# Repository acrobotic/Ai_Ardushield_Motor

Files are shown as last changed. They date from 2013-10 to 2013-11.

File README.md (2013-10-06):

Overview
---
This repository includes the Eagle design files (schematics and layout) for our
[Motor Shield for the Arduino Uno][1]. The shield design is based on two ICs:
the Toshiba TB6612FNG dual motor driver and the NXP PCA9685 16-bit PWM
generator.  The TB6612FNG uses the PWM signals generated by the PCA9685 to set
the speed and direction of the motor(s) connected to its output.  The PWM
signals are set by the commands sent from the Arduino to the PCA9685
via I2C.

The shield includes 2 motor driver chips, so it's able to control up to 4
bi-directional DC motors, 2 stepper motors (uni- or bi-polar), or a combination
of the two types.  

The PWM chip is controlled via I2C, which allows the shield to be stackable.
By setting each shield on the stack to a different I2C address we can control
(in theory) up to 32 of these shields with a single Arduino.

A couple of standard 3-pin headers are readily available on the board for
connecting servo motors directly to pins D8 and D9 on the Arduino.

The firmware files along with code samples are also included in this
repository.

This product was heavily inspired by the [Adafruit Motor/Stepper/Servo Shield
for Arduino][2], and it's released under a (hopefully) compatible open-source
license detailed below.

Product page
---
Please consider buying products from Acrobotic to help fund future Open-Source
projects like this! We'll always put our best effort in every project, and
release all our design files and code for you to use.

[Tutorials, technical details, and more information about this product can be
found here: http://acrobotic.com/catalog/product/view/id/63][1]

License Information
---

All contents of this repository are licensed under a [Creative Commons
Attribution-ShareAlike 3.0 Unported
License](http://creativecommons.org/licenses/by-sa/3.0/).



[1]: http://acrobotic.com/catalog/product/view/id/63 "Ardushield Motor"
[2]: http://www.adafruit.com/products/1438 "Adafruit Motor/Stepper/Servo Shield for Arduino"

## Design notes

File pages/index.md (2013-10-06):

---
layout: page
title: Ai Ardushield Motor
tagline: Board design files and example firmware for the Acrobotic Motor Shield (Arduino Uno).
github_project: Ai_Ardushield_Motor
github_user_url: https://github.com/acrobotic
---
{% include JB/setup %}
{% include INCLUDE.md %}

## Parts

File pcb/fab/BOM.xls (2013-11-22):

Ai Ardushield Motor – BOM
Cisco Zabala (x1sc0@acrobotic.com) last updated: 22.11.2013
Manufacturer | Manuf. Part Number | Vendor | Vendor Part Number | Type | Designator | Qty | Description | Case | SMD, BGA, LCC, OR TH | Notes
Stackpole Electronics Inc | RMCF0603JT1K00 | Digi-Key | RMCF0603JT1K00CT-ND | Resistors | R1 | 1 | RES 1K OHM 1/10W 5% 0603 | 0603 | SMD
Stackpole Electronics Inc | RMCF0603JT10K0 | Digi-Key | RMCF0603JT10K0CT-ND |  | R2, R3, R4, R5, R6, R7, R8 | 7 | RES 10K OHM 1/10W 5% 0603 | 0603 | SMD
Panasonic Electronic Components | EEE-1CA101WP | Digi-Key | PCE3880CT-ND | Capacitors | C1 | 1 | CAP ALUM 100UF 16V 20% SMD | PANASONIC-C | SMD
Panasonic Electronic Components | EEE-1CA470WR | Digi-Key | PCE3890CT-ND |  | C2, C3 | 2 | CAP ALUM 47UF 16V 20% SMD | PANASONIC-C | SMD
Yageo | CC0603ZRY5V9BB104 | Digi-Key | 311-1343-1-ND |  | C4, C5, C6 | 3 | CAP CER 0.1UF 50V Y5V 0603 | 0603 | SMD
TDK Corporation | C1608X5R1A106M080AC | Digi-Key | 445-6853-1-ND |  | C7, C8 | 2 | CAP CER 10UF 10V 20% X5R 0603 | 0603 | SMD
NXP |  | Digi-Key | 568-5931-1-ND | ICs | IC1 | 1 | IC PWM CTLR LED DVR 28TSSOP | 28TSSOP | SMD
Toshiba |  | Digi-Key | TB6612FNG(OC8EL)CT-ND | IC | IC2, IC3 | 2 | IC MOTOR DRIVER PAR 24SSOP | 24SSOP | SMD
OSRAM | LB Q39E-N1P1-35-1 | Digi-Key | 475-2815-1-ND | LEDs | ON | 1 | LED CHIPLED BLUE 470NM 0603 SMD | 0603 | SMD
Alpha & Omega Semiconductor | AOD417 | Digi-Key | 785-1106-1-ND | Discrete | Q1 | 1 | MOSFET P-CH -30V -25A TO-252 | TO-252-3 | SMD
TE Connectivity | 2-1437565-9 | Digi-Key | 450-1792-1-ND | Buttons | SW1 | 1 | SWITCH TACTILE SPST-NO 0.05A 12V | 6mm x 6mm | SMD
 |  | Acrobotic | CON-00007 | Connectors | J1, J7, J8, J10 | 4 | 2-Pin Screw Terminal Block (3.5mm) |  | TH
 |  | Acrobotic | CON-00011 |  | J7, J8 | 2 | 3-Pin Screw Terminal Block (3.5mm) |  | TH
 |  | Acrobotic | CON-00010 |  | J2 | 1 | 0.1” Pitch, 2-Row, 6-Pin (Male) |  | TH
 |  | Acrobotic | CON-00009 |  | J3, J4, J5, J6, JP1. JP2 | 1-2 | 0.1” Pitch, 40-Pin (Male) |  | TH | Easily cut to length
 |  | - | - |  | J9 | - | - | - | - | Left open for user
 |  | Acrobotic | CON-00008 |  | (JP1, JP2) | 2 | 2-Pin Jumper |  | - | For power selection

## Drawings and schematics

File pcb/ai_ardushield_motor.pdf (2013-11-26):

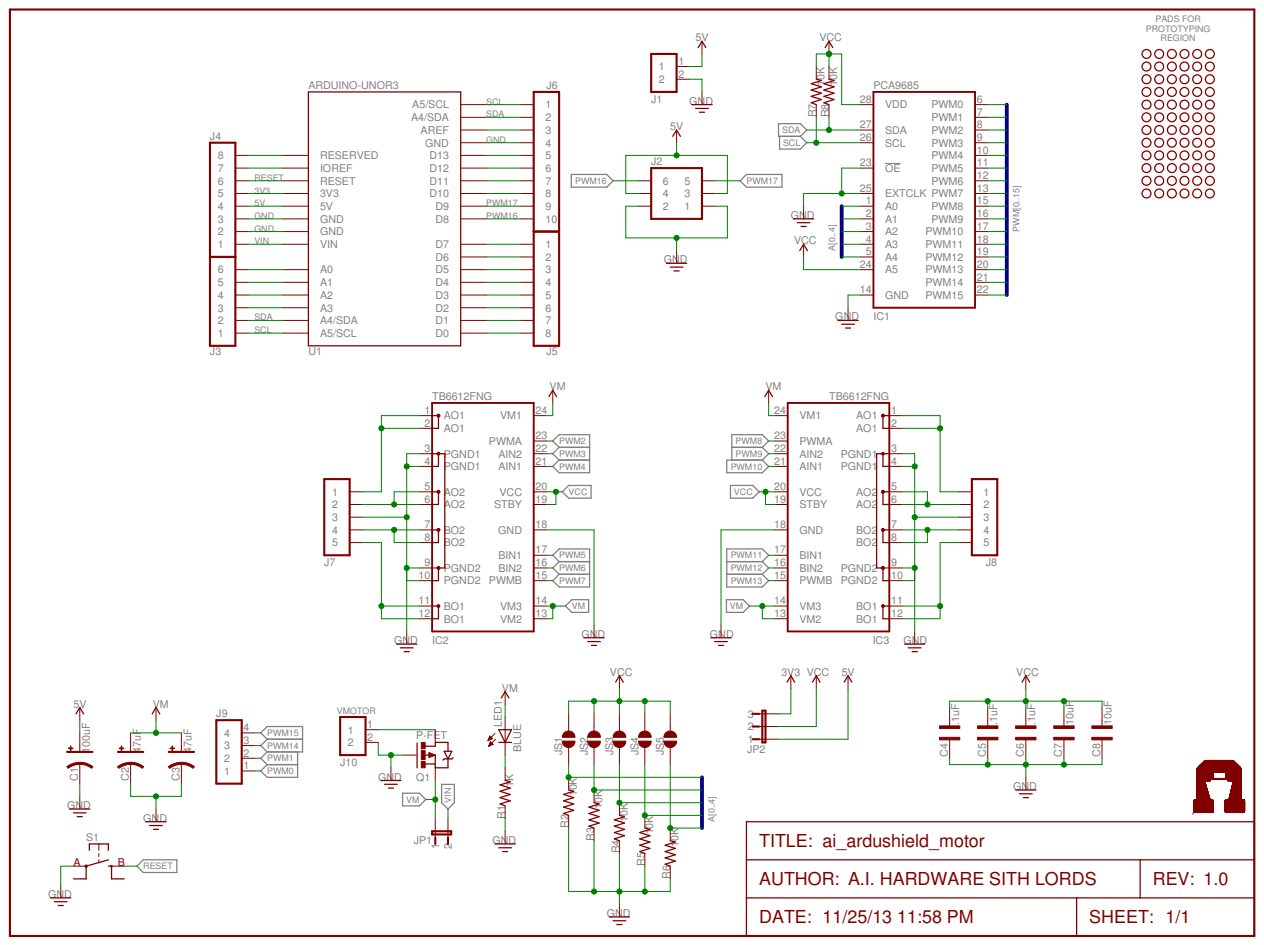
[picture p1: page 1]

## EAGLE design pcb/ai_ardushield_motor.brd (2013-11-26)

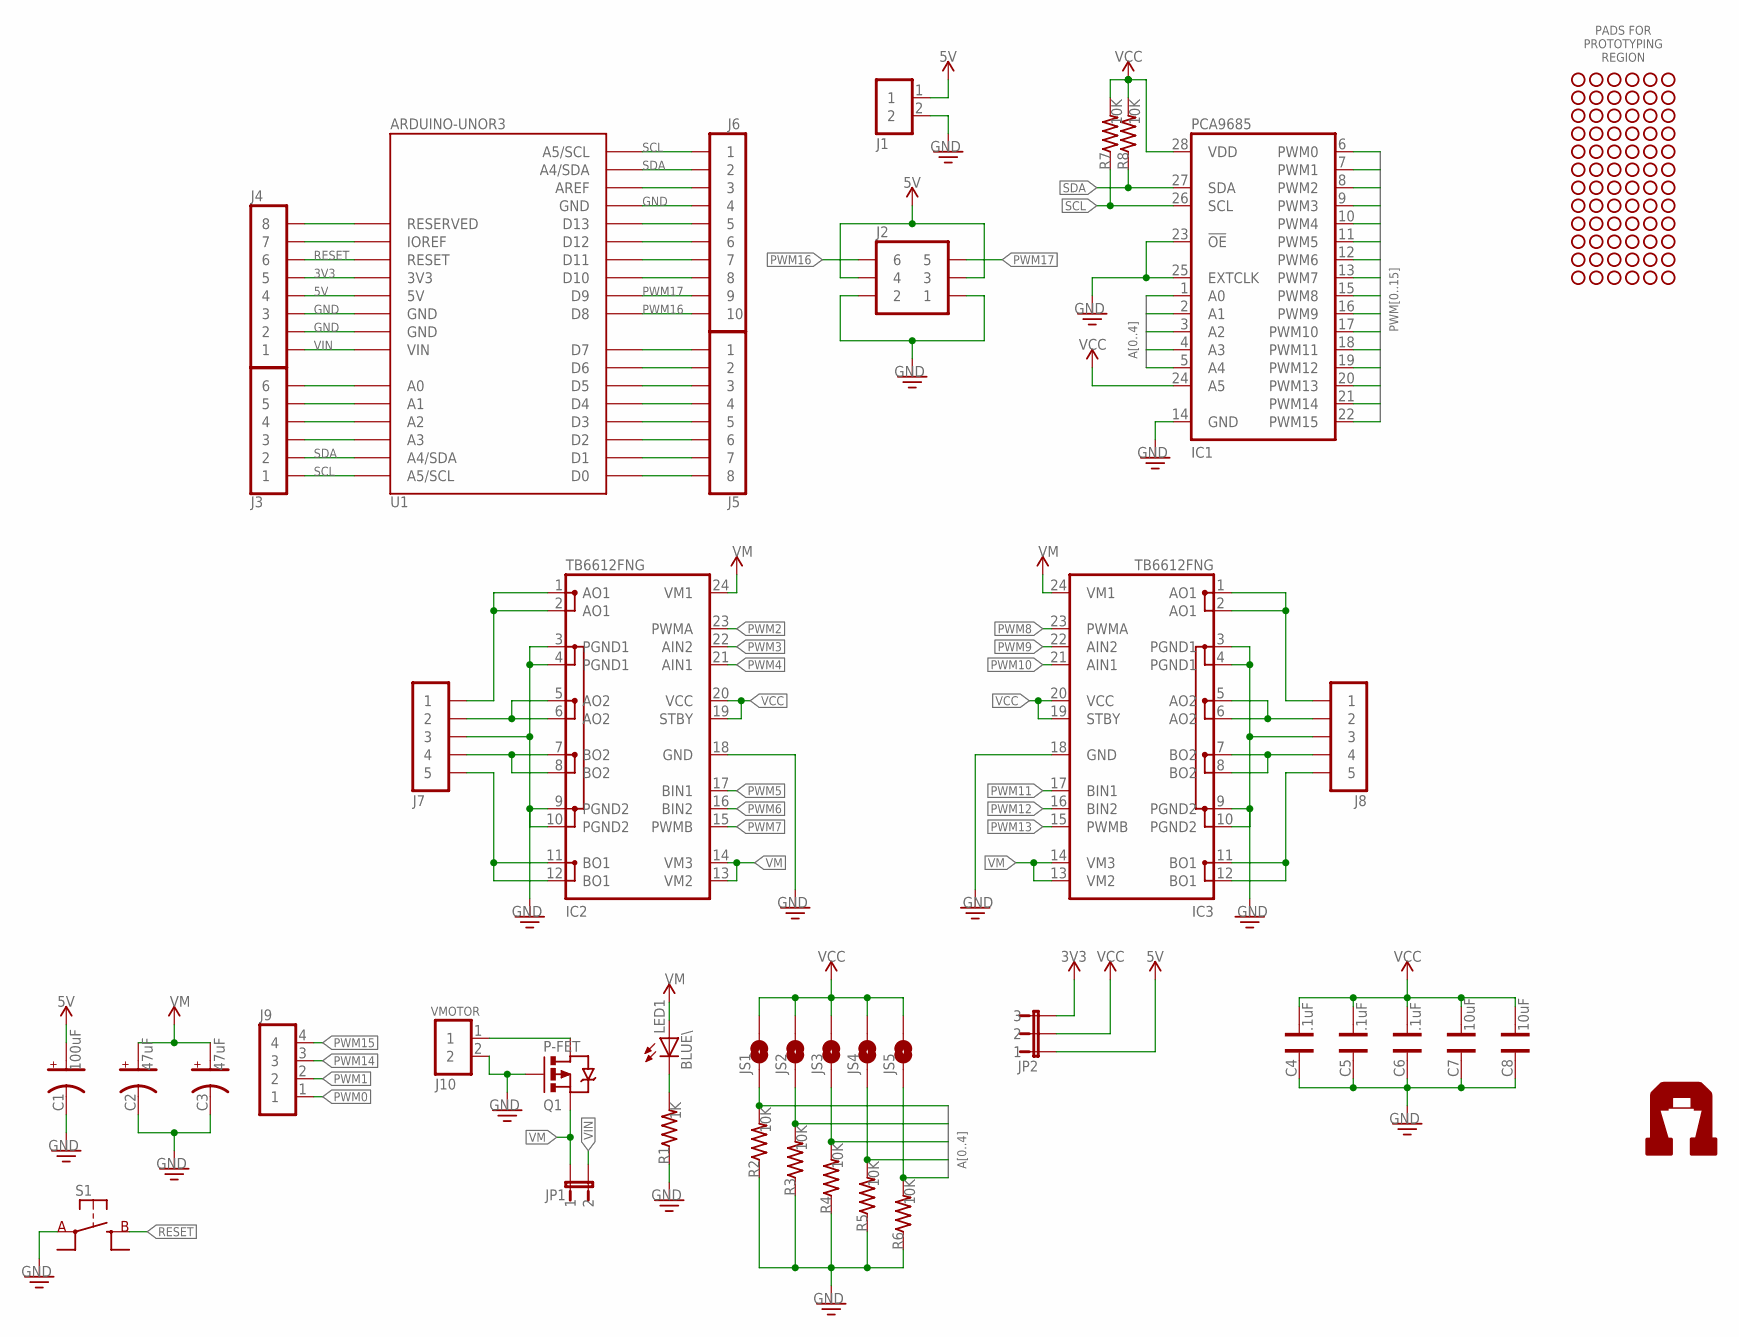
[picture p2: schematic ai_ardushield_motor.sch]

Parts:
C1: 100uF; CAP-PANASONIC-C
C2, C3: 47uF; CAP-PANASONIC-C
C4, C5, C6: .1uF; CAP-0603
C7, C8: 10uF; CAP-0603
IC1: PCA9685; TSSOP28
IC2, IC3: TB6612FNG; SSOP24
J1, J10: 1X02ST; 1X02-ST
J2: 2X03
J3: 1X06
J4, J5: 1X08
J6: 1X10
J7, J8: 1X05ST; 1X05-ST
J9: 1X04
J11, J12, J13, J14, J15, J16, J17, J18, J19, J20, J21, J22: 1X06-PROTO; 1X06-NOFIRST
JP1: 1X02-PJ; 1X02
JP2: 1X03-PJ; 1X03
JS1, JS2, JS3, JS4, JS5: 1X02-SJNO; 1X02-SJ-NO
LED1: BLUE\; LED-0603
Q1: P-FET; TO252
R1: 1K; RES-0603
R2, R3, R4, R5, R6, R7, R8: 10K; RES-0603
S1: SW-SPSTSMD06X06; SW-SPST-SMD06X06
U1: ARDUINOUNOR3; UNOR3
U$14: AI-LOGOL; AI-LOGO-L

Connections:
3V3: J4.5, JP2.3, U1.3V3
5V: C1.A, J1.1, J2.3, J2.4, J4.4, JP2.1, U1.5V
A0: IC1.1 (A0), JS1.1, R2.2
A1: IC1.2 (A1), JS2.1, R3.2
A2: IC1.3 (A2), JS3.1, R4.2
A3: IC1.4 (A3), JS4.1, R5.2
A4: IC1.5 (A4), JS5.1, R6.2
GND: C1.C, C2.C, C3.C, C4.2, C5.2, C6.2, C7.2, C8.2, IC1.14 (GND), IC1.23 (!OE), IC1.25 (EXTCLK), IC2.3 (PGND1), IC2.4 (PGND1), IC2.9 (PGND2), IC2.10 (PGND2), IC2.18 (GND), IC3.3 (PGND1), IC3.4 (PGND1), IC3.9 (PGND2), IC3.10 (PGND2), IC3.18 (GND), J1.2, J2.1, J2.2, J4.2, J4.3, J6.4, J7.3, J8.3, J10.2, Q1.G, R1.1, R2.1, R3.1, R4.1, R5.1, R6.1, S1.A@1 (A), S1.A@2 (A), U1.GND@1 (GND), U1.GND@2 (GND), U1.GND@3 (GND)
unnamed: J5.1, U1.D7
unnamed: J5.2, U1.D6
unnamed: LED1.C, R1.2
unnamed: J3.3, U1.A3
unnamed: J3.4, U1.A2
unnamed: J3.5, U1.A1
unnamed: J3.6, U1.A0
unnamed: J4.7, U1.IOREF
unnamed: J4.8, U1.RESERVED
unnamed: J5.3, U1.D5
unnamed: J5.4, U1.D4
unnamed: J5.5, U1.D3
unnamed: J5.6, U1.D2
unnamed: J5.7, U1.D1
unnamed: J5.8, U1.D0
unnamed: IC2.1 (AO1), IC2.2 (AO1), J7.1
unnamed: IC2.5 (AO2), IC2.6 (AO2), J7.2
unnamed: J6.3, U1.AREF
unnamed: J6.5, U1.D13
unnamed: J6.6, U1.D12
unnamed: J6.7, U1.D11
unnamed: J6.8, U1.D10
unnamed: IC2.7 (BO2), IC2.8 (BO2), J7.4
unnamed: IC2.11 (BO1), IC2.12 (BO1), J7.5
unnamed: IC3.1 (AO1), IC3.2 (AO1), J8.1
unnamed: IC3.5 (AO2), IC3.6 (AO2), J8.2
unnamed: IC3.7 (BO2), IC3.8 (BO2), J8.4
unnamed: IC3.11 (BO1), IC3.12 (BO1), J8.5
PWM0: IC1.6 (PWM0), J9.1
PWM1: IC1.7 (PWM1), J9.2
PWM2: IC1.8 (PWM2), IC2.23 (PWMA)
PWM3: IC1.9 (PWM3), IC2.22 (AIN2)
PWM4: IC1.10 (PWM4), IC2.21 (AIN1)
PWM5: IC1.11 (PWM5), IC2.17 (BIN1)
PWM6: IC1.12 (PWM6), IC2.16 (BIN2)
PWM7: IC1.13 (PWM7), IC2.15 (PWMB)
PWM8: IC1.15 (PWM8), IC3.23 (PWMA)
PWM9: IC1.16 (PWM9), IC3.22 (AIN2)
PWM10: IC1.17 (PWM10), IC3.21 (AIN1)
PWM11: IC1.18 (PWM11), IC3.17 (BIN1)
PWM12: IC1.19 (PWM12), IC3.16 (BIN2)
PWM13: IC1.20 (PWM13), IC3.15 (PWMB)
PWM14: IC1.21 (PWM14), J9.3
PWM15: IC1.22 (PWM15), J9.4
PWM16: J2.6, J6.10, U1.D8
PWM17: J2.5, J6.9, U1.D9
RESET: J4.6, S1.B@1 (B), S1.B@2 (B), U1.RESET
SCL: IC1.26 (SCL), J3.1, J6.1, R7.1, U1.A5/SCL@1 (A5/SCL), U1.A5/SCL@2 (A5/SCL)
SDA: IC1.27 (SDA), J3.2, J6.2, R8.1, U1.A4/SDA@1 (A4/SDA), U1.A4/SDA@2 (A4/SDA)
VCC: C4.1, C5.1, C6.1, C7.1, C8.1, IC1.24 (A5), IC1.28 (VDD), IC2.19 (STBY), IC2.20 (VCC), IC3.19 (STBY), IC3.20 (VCC), JP2.2, JS1.2, JS2.2, JS3.2, JS4.2, JS5.2, R7.2, R8.2
VIN: J4.1, JP1.2, U1.VIN
VM: C2.A, C3.A, IC2.13 (VM2), IC2.14 (VM3), IC2.24 (VM1), IC3.13 (VM2), IC3.14 (VM3), IC3.24 (VM1), JP1.1, LED1.A, Q1.S
VMOTOR: J10.1, Q1.D

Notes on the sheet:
VMOTOR
PADS FOR PROTOTYPING REGION

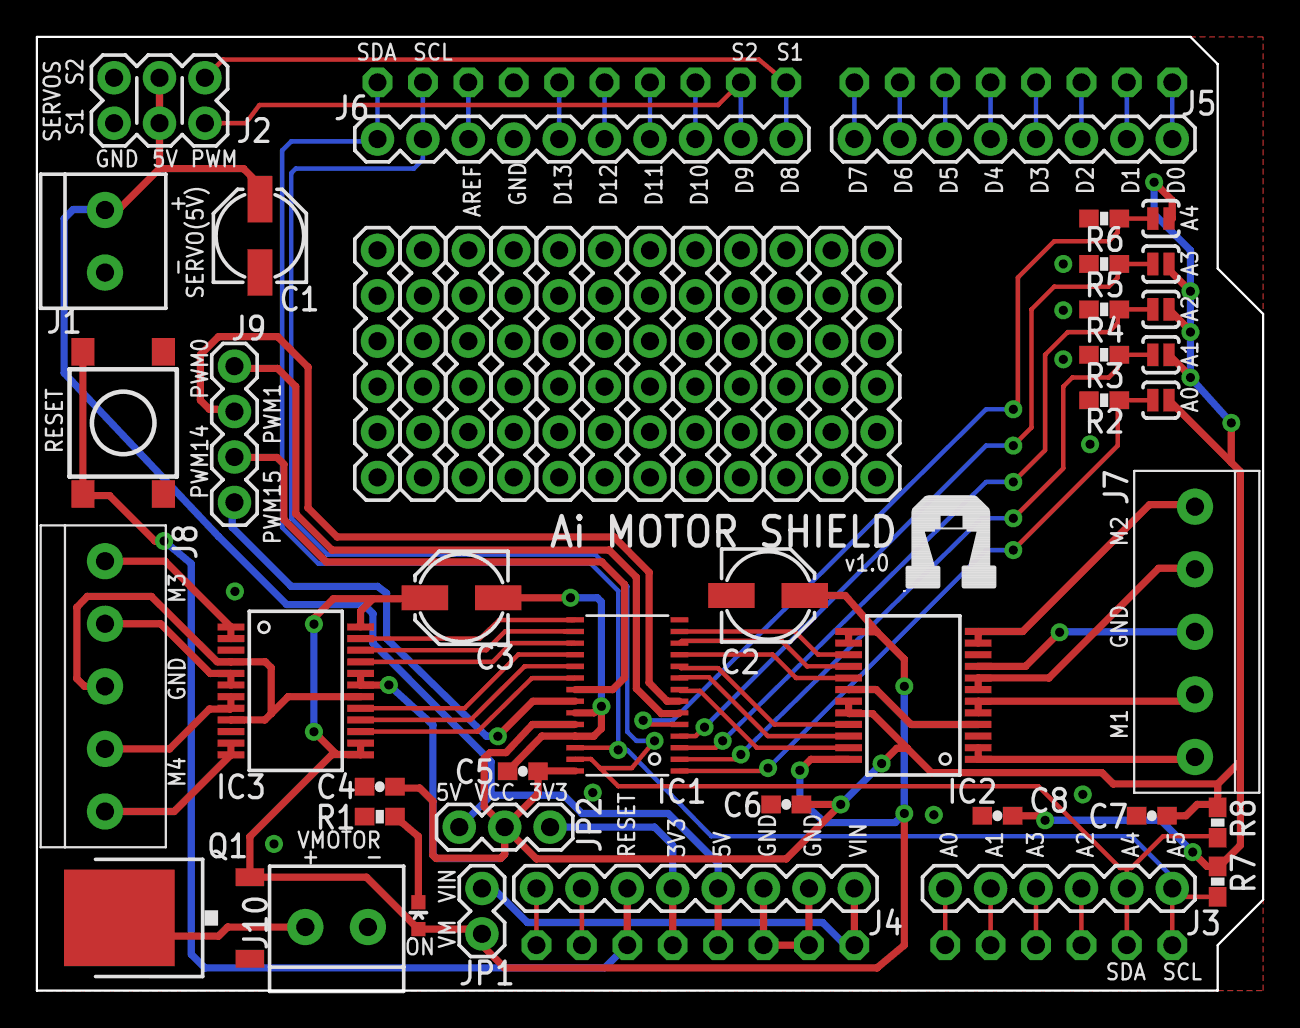
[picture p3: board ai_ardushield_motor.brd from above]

Board: 2 copper layers, 68.6 x 53.3 mm, 53 parts (0 on the bottom side), 61 nets.

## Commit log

2013-07-25 First commit.
    [BOM.xls, ai_ardushield_motor.brd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]
2013-07-25 Fixed a few minor warnings in the ERC.
    [ai_ardushield_motor.brd, ai_ardushield_motor.sch]
2013-07-25 changed the pcb dimension width.
    [ai_ardushield_motor.brd, ai_ardushield_motor.sch]
2013-10-06 New version including detailed BOM
    [BOM.xls, ai_ardushield_motor.brd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]
2013-10-08 Fixed typo in BOM
    [BOM.xls]
2013-10-15 updated BOM and gerbers
    [BOM.xls]
2013-11-22 minor typo on BOM
    [BOM.xls]
2013-11-26 Updated to use latest libraries.
    [ai_ardushield_motor.brd, ai_ardushield_motor.sch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]
